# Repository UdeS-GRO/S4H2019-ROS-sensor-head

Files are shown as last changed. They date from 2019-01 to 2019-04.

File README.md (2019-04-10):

# 3-axes-Camera-ROS

## Introduction

3 axis head system that can be controlled by a cell phone or a USB controller. This open-source project is part of the Robotics Engineering Project Course at the Université de Sherbrooke.

Useful links: 

- http://emanual.robotis.com/docs/en/software/dynamixel/dynamixel_workbench/#ros
- http://emanual.robotis.com/docs/en/parts/controller/opencr10/#install-on-linux
- https://github.com/GoldenCheetah/GoldenCheetah/wiki/Allowing-your-linux-userid-permission-to-use-your-usb-device

# 1- Linux configuration

## Update

If you start from a clean Linux install, please do the following commands. 

```bash
$ sudo apt-get update
$ sudo apt-get upgrade
```

## USB Port Permissions

In order to communicate with the OpenCR card via USB, the user has to be added to the correct group. This [link](https://github.com/GoldenCheetah/GoldenCheetah/wiki/Allowing-your-linux-userid-permission-to-use-your-usb-device) shows all the details about this modification. But don't forget this part: **Important: the computer needs to be restarted to have the modifications applied.**

```bash
[user@machine ~]$ sudo usermod -a -G dialout user
```

## Arduino IDE

See http://emanual.robotis.com/docs/en/parts/controller/opencr10/#install-on-linux for instructions to use the full and latest version of the Arduino IDE, not the one in the packages repository since it might be updated.

# 2- OpenCR board configuration

To be able to control the Dynamixel motors via ROS, the OpenCR card need to be converted in a USB to Serial device that will make the bridge between the ROS server (on Linux) and the motors connected with the OpenCR card. 

After Arduino IDE is run, click File → Preferences in the top menu of the IDE. When the Preferences window appears, copy and paste the following link to the Additional Boards Manager URLs text box.

```bash
https://raw.githubusercontent.com/ROBOTIS-GIT/OpenCR/master/arduino/opencr_release/package_opencr_index.json
```

Then, click Tools → Board → Boards Manager. Type OpenCR into the text box to find the OpenCR by ROBOTIS package. When you find it, click Install. After the installation, “INSTALLED” will appear on your screen. See if the OpenCR Board is now on the list of Tools → Board. Click this to import the OpenCR Board source.

## Code upload

In order to the OpenCR card to make the bridge, please upload `usb_to_dxl` firmware (`File` -> `Examples` -> `OpenCR` -> `10.Etc` -> `usb_to_dxl`) Then you can use `/dev/ttyACM0` port (The number of the port may be different depending on setup).

## Hardware

In order to test the motors, please connect a SINGLE motor, connect the power supply and power on the card. 

# 3- ROS Installation

You can follow this [link](http://emanual.robotis.com/docs/en/software/dynamixel/dynamixel_workbench/) for the installation tutorial. The ROS utilization corresponds to the section 5 of the tutorial. Below are the condensed steps that need to be taken. Below are the simplified steps. 

## Install ROS on PC

The following script will allow you to simplify the ROS installation procedure. Run the following command in a terminal window. 

```bash
wget https://raw.githubusercontent.com/ROBOTIS-GIT/robotis_tools/master/install_ros_kinetic.sh && chmod 755 ./install_ros_kinetic.sh && bash ./install_ros_kinetic.sh
```

**After install ROS, please reboot PC**

## Download ROS Packages

Once ROS is installed, you'll need to change the directory to catkin_ws/src. It is where all the ROS package will be installed. 

```bash
cd ~/catkin_ws/src
```

**Main packages**

```bash
git clone https://github.com/ROBOTIS-GIT/dynamixel-workbench.git
git clone https://github.com/ROBOTIS-GIT/dynamixel-workbench-msgs.git
```

**Dependant packages**

```bash
git clone https://github.com/ROBOTIS-GIT/DynamixelSDK.git
git clone https://github.com/ROBOTIS-GIT/open_manipulator_msgs.git
sudo apt-get install ros-kinetic-moveit-core ros-kinetic-moveit-ros-planning ros-kinetic-moveit-ros-planning-interface
```

**Install this package**

Still in the ```catkin_ws/src/``` folder, clone this project.
```bash
git clone https://github.com/gene2302/3-axis-ROS-sensor-head.git
```

Once all the git has been cloned, different ROS packages will be installed too. 

## ROS Initilization

First, you'll need to source the correct ROS workspace in order to use ROS from anywhere. Then, make sure all dependencies are installed by using the rosdep tool. Finally, run catkin_make to build all the ROS workspace. 

```bash
source /opt/ros/kinetic/setup.bash
cd ~/catkin_ws
sudo apt-get update
rosdep install --from-paths src --ignore-src -r -y
catkin_make
```

If you are using a Raspberry Pi or a computer low on memory, you might need to limit the number of build threads jobs launched my catkin_make. By default, catkin_make launches one job (thread) per processor core. The `-j 1` argument and value specifies to run one job. It will be slower, but will compile.

```bash
source /opt/ros/kinetic/setup.bash
cd ~/catkin_ws
sudo apt-get update
rosdep install --from-paths src --ignore-src -r -y
catkin_make -j 1
```

# 4- ROS Use for a single motor

## Find the Dynamixels connected to the OpenCR card. 

In order to see which Dynamixel motors are connected, this command needs to be executed. Change ''ACM0'' to the port used by the OpenCR card. 

```bash
rosrun dynamixel_workbench_controllers find_dynamixel /dev/ttyACM0
```

## Control a SINGLE motor with ROS (command line)

**WARNING**: This package is intended for `SINGLE` Dynamixel. Please connect only `One(1)` Dynamixel to your device. If you connect multiple Dynamixels, manager would detect the **lowest ID** among connected Dynamixels. This package is to check Dynamixel status and access Dynamixel’s control table. 

## Control a SINGLE motor with ROS (GUI)

Important: In order to connect this node with the connect USB port, you shall modify the port in the configuration file located in the dynamixel_workbench_controllers config file. When using the ```sensor_head_gui``` package, the dynamixel_workbench_controllers configuration file does not need to be changed here, as it is supplied by the ```sensor_head_gui.launch``` file located in  ```ROS/sensor_head_gui/launch/sensor_head_gui.launch```

```bash
roslaunch dynamixel_workbench_single_manager single_manager.launch
```

This package is to check Dynamixel status and access Dynamixel’s Control Table addresses via **GUI**. **WARNING**: Before you run this package, please launch [single_manager](http://emanual.robotis.com/docs/en/software/dynamixel/dynamixel_workbench/#single-manager) first.

```
rosrun dynamixel_workbench_single_manager_gui dynamixel_workbench_single_manager_gui
```

# 5- Using "sensor_head_gui" package

In order to use the package, please launch this launch file.

```
roslaunch sensor_head_gui base_launch.launch
```

This file will launch several ROS nodes (dynamical_workbench_controllers, sensor_head_gui). If you can't find the package, please see https://answers.ros.org/question/190317/ros-cant-find-package/

The arguments in this file, as well as the two .yaml configuration files in the ```ROS/sensor_head_gui/config/``` folder, can be modified with other values if your setup is different.

Before the first run, a certificate must be created to be able to use a secured (https) website, required to use motion sensors on a mobile device. Create a SSL certificate by filling out the answers to the informations asked by the program, and make sure to use the exact name (address) that will be used at the FQDN or YOUR name question:
```
cd ~ && openssl req -new -x509 -keyout s4e4gro.pem -out s4e4gro.pem -days 365 -nodes
```

Using a https connection is required to use the orientation and motion javascript interfaces, or else they do not work, since it was deprecated. The certificate file is not included in the source control. 

You can now open a browser to "https://localhost:4443" or replace localhost with the host's IP adress, or the computer's name if the full names are resolved. Adding the https is important.

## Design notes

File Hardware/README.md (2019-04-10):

# Assembly Process

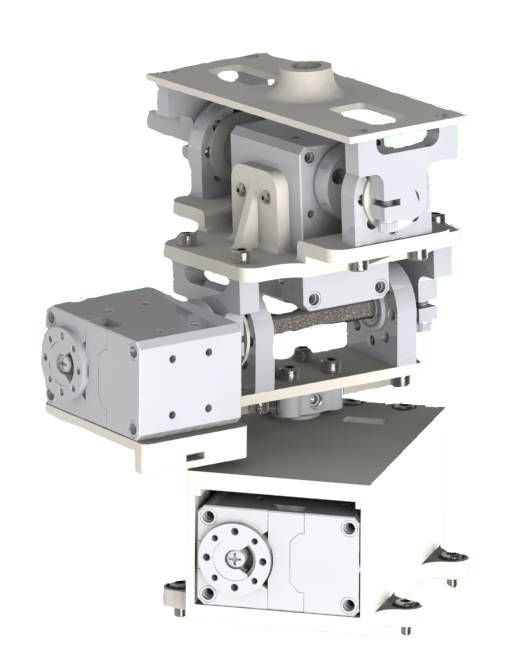
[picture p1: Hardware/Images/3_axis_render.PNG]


## 1 - Download BOM.
Download the build of material, follow this link : 
[Excel BOM](https://github.com/gene2302/3-axis-ROS-sensor-head/blob/master/Hardware/BOM/Master_parts_list.xlsx)

## 2 - Purchase required standards parts.

You need purchase some standard parts from Servocity, Dynamixel and McMaster for exemple. All links are in the BOM excel.

## 3 - 3D print all 3d printed parts

You need to print all pieces and respect qty. 

Caracteritics for PLA printing:

Layer high : 0,2mm
Extruder temp: 195-205 degC
Infill : 10 to 60 % Diamond infill

## 4 - Assembly the Z module:

Take the Z motor, fix the adapter_gear on the motor with 4 screws m2.5.
Fix the bevel_gear on it. Screw the motor with the base. Fix the other bevel-gear on the 2in shaft. Place one bearing in the bearing hole. Place the other bearing in the top plate bearing hole. This is "pressfit" hole.
Finaly, join top plate with the base and srew it with 3X m3 SHCS.
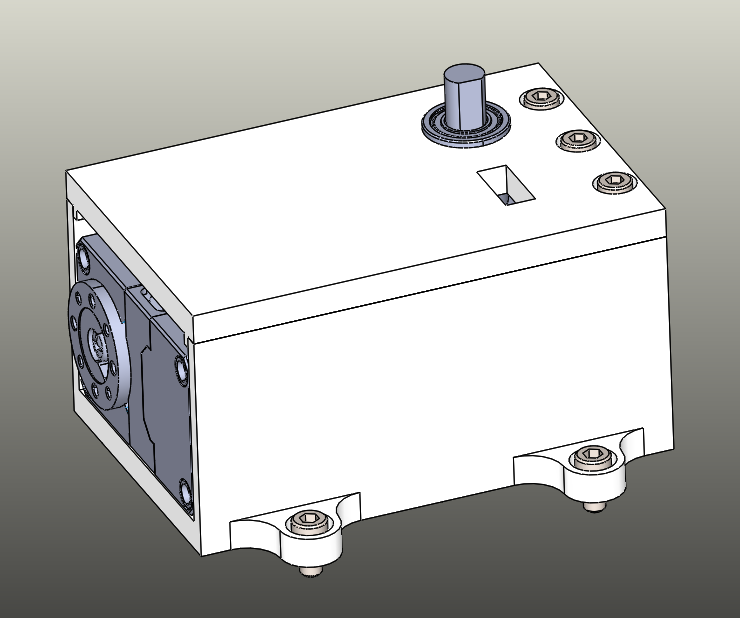
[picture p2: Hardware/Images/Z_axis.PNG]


## 5 - Assembly the X module:

Take the X motor (XM-430-w350) and screw the motor adaptor (item no ...). Place bearing support (2x) and spacer with screw #6-32(2x). Screw the shaft adaptor under the 3d printed piece with 4x #6-32.
Align shaft, bearing, spacer and ring for complete the assy.
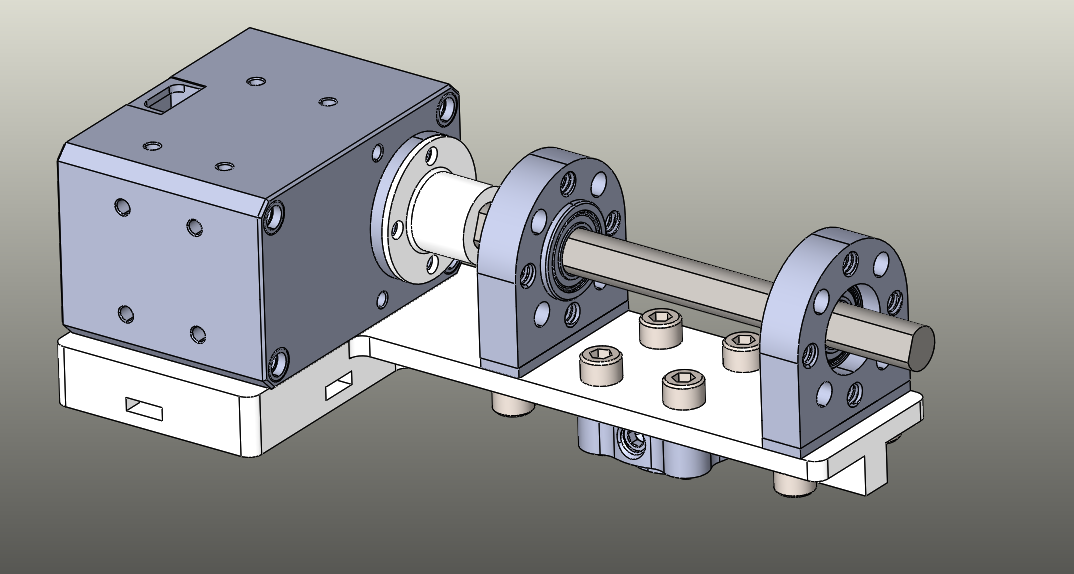
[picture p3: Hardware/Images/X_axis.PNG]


## 6 - Assembly the Y module:

Take the Y motor(XM-430-w250) and screw the motor adaptor on it. Plug 1in shaft in the adaptor motor. Next, screw 2x bearing supports and 2x bore bottom with the 3d printed y-plate (#6-32). Place the other shaft with a collet and spacer.
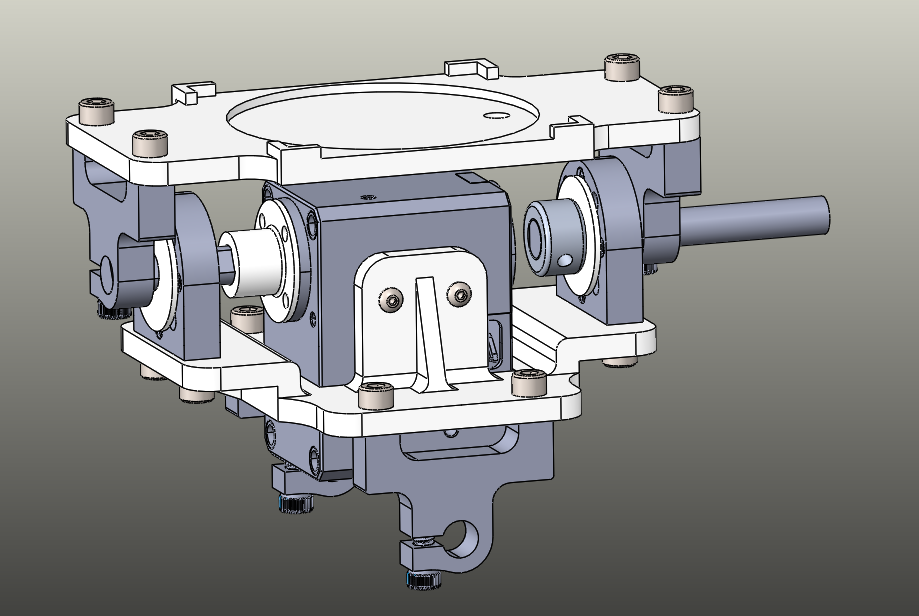
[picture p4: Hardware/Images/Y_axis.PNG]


## 7 - Assembly the full module.

Take all the modules and assemble them together with appropriates screws according with the picture.
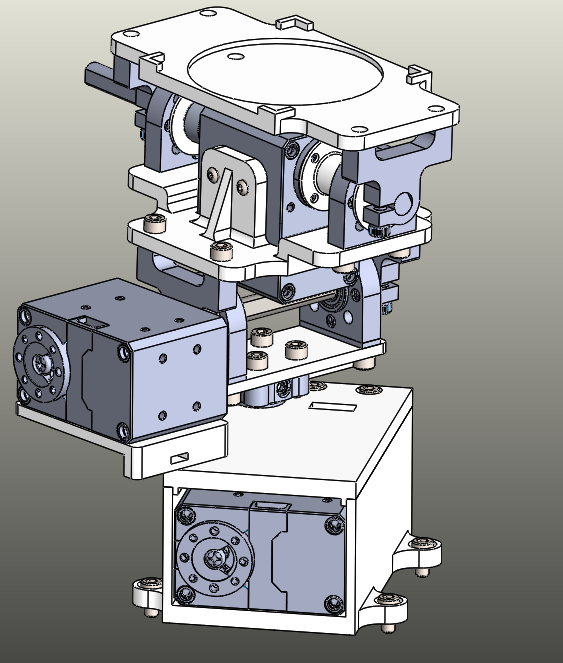
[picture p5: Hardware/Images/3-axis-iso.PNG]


<!--stackedit_data:
eyJoaXN0b3J5IjpbLTE4NjkwNDc1NTUsLTM2NjI4Njg2MSw0ND
A3NjIyMTcsLTIyNjI0MTQwMiwtMjM4MTM3MzU2LC0xNDYwMzQ3
OTA3LC0xMjY1MTA3ODQ0LDE3ODg3OTc0MDMsMTkyMTkzNDQ0Ny
wtNTU0MDY0NjA2LC0zNDU2NDMzNDQsMTEyMDA1NTk5XX0=
-->

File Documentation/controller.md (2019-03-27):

http://wiki.ros.org/joy/Tutorials/ConfiguringALinuxJoystick

Install the xbox controller driver with:
```bash
sudo apt-get install xboxdrv
```

Add controller in the USB ports of Virtualbox
Check if it is there with 
```bash
lsusb
```
then install joy with
```bash
sudo apt-get install ros-kinetic-joy
ls /dev/input/
```

Test to see which port your controller is attached to like this for example:

```bash
sudo jstest /dev/input/js2
```
Here's the mapping for our Xbox One Controller
* Axes:
	* 0: Left Joystick L/R (Analog) L = 1, R = -1
	* 1: Left Joystick U/D (Analog) U = 1, D = -1
	* 2: LT (Analog) Not pressed = 1 Max = -1
	* 3: Right Joystick L/R (Analog)
	* 4: Right Joystick U/D (Analog)
	* 5: RT (Analog)
	* 6: Cross L/R (Digital)
	* 7: Cross U/D (Digital)

* Buttons (Digital): (0 or 1)
	* 0: A
	* 1: B
	* 2: X
	* 3: Y
	* 4: L
	* 5: R
	* 6: Back
	* 7: Start
	* 8: Power
	* 9: Pressing Left Joystick
	* 10: Pressing Right Joystick

You have to make the joystick accesible to ROS with:

```bash
sudo chmod a+rw /dev/input/js2
ls -l /dev/input/js2
```

then run joy to see values of your axes and buttons that should be between -1 and 1

In different terminals, run:
```bash
roscore
```
```bash
rosparam set joy_node/dev "/dev/input/js2"
rosrun joy joy_node
``` 
and
```bash
rostopic echo joy
```

then follow the tutorial at: http://wiki.ros.org/joy/Tutorials/WritingTeleopNode
but add 
```bash
catkin_package()
```
in the CMakeLists.txt file

also do a

```bash
catkin_make
```
and source your bash

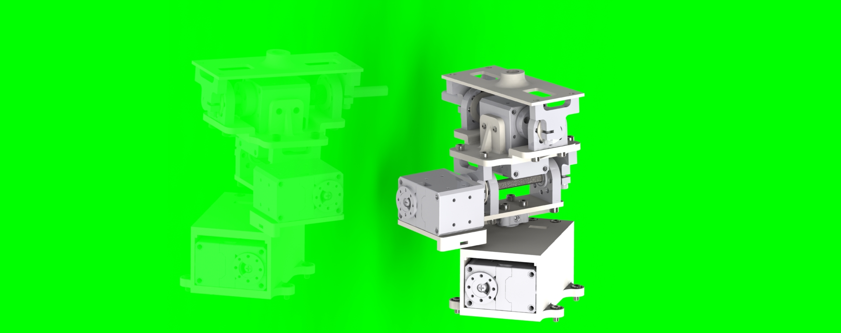
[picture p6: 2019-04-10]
Hardware/Images/rendu vert.JPG

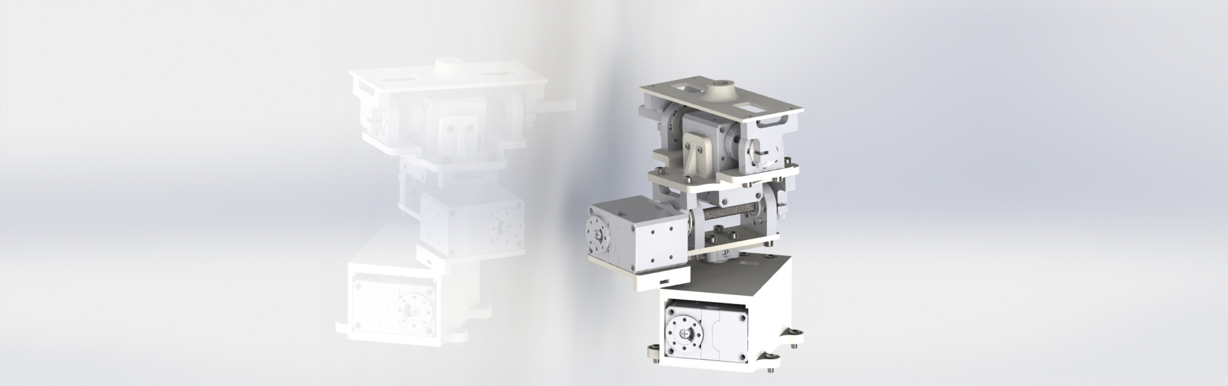
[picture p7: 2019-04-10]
Hardware/Images/rendu blanc.JPG

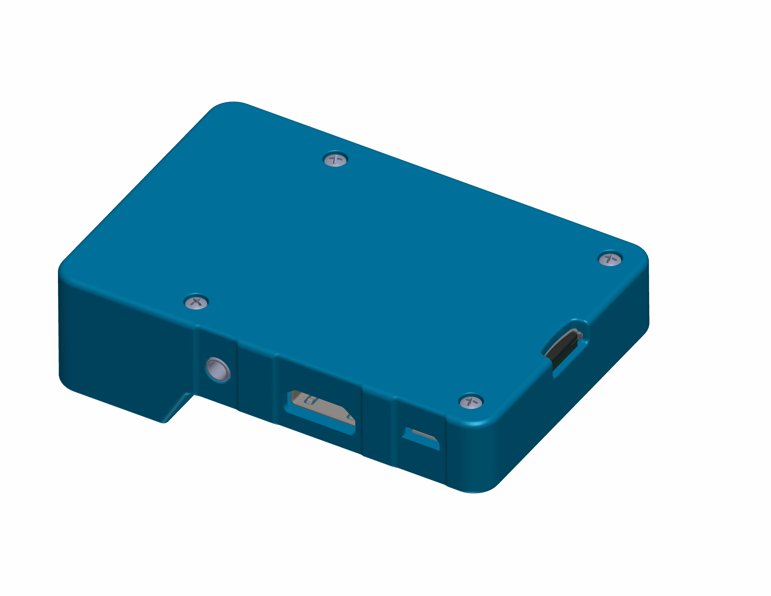
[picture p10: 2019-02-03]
Hardware/CAD/raspberry-pi-b-case-1.snapshot.3/RPI B+ Case Bottom View.JPG

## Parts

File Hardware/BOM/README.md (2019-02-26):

## Build of materiel:

This is the BOM for assembly the head module. 
You can buy all stuf by internet, follow links in the excel.

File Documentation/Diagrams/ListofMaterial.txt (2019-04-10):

List of material:
Raspberry Pi 3B+
USB Camera (We used Microsoft LifeCam VX-2000)
OpenCR 1.0
Dynamixel Motor XL430-W250-T (2)
Dynamixel Motor XM430-W350-T
Xbox One Controller
Android Cell Phone
Mouse
Screen
Keyboard

Raspberry Pi Power Supply (Type A - Micro-USB)
OpenCR Power Supply (Type A - Coaxial)
3-pin connector(3)
USB-USB cable
HDMI-HDMI cable

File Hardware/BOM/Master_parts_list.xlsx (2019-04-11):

The cost information contained in this document is of a budgetary and planning nature and is intended for informational purposes only.
Author: Etienne Gendron, Robotic engineering |  |  |  |  |  |  |  | Total | $473.08
University of Sherbrooke, QC, CAN
Part | Qty in sub-assy | Qty to Print | Qty In project | Brand | Ref | Model/Config (If applicable) | Project Section | Price | Cost to Project | Link
Z_Assy | - | - | 1
Z_base | - | 1 | 1 | 3Dprinting |  |  |  | $12.00 | $12.00
Cover | - | 1 | 1 | 3Dprinting |  |  |  | $6.00 | $6.00
adapter moteur-gear | - | 1 | 1 | 3Dprinting |  |  |  | $1.00 | $1.00
bearing | 2 | - | 6 | Servocity | 535198 |  | 5.78 $ | $2.89 | $17.34 | https://www.servocity.com/0-250-id-x-0-500-od-flanged-ball-bearing
XL-430-w250 | 1 | - | 2 | Dynamixel |  |  | 49.90 $ | $49.90 | $99.80 | http://www.robotis.us/dynamixel-xl430-w250-t/
gear_45 | 2 | - | 2 | Servocity | 615406 |  | 11.98 $ | $5.99 | $11.98 | https://www.servocity.com/6mm-bevel-gears
shaft_0.25-2 | 1 | - | 1 | Servocity | 634068 |  | 1.49 $ | $1.49 | $1.49
SHCS (B18.3.1M - 2.5 x 0.45 x 5) | 4 | - | 4 | hardware
SHCS (B18.3.1M - 3 x 0.5 x 5) | 3 | - | 3 | hardware
HEX_NUT_M3 | 3 | - | 3 | hardware
HX-SHCS (0.138-32x0.25x0.25-N) | 4 | - | 4 | hardware
X_Assy |  |  | 1
X_base_3.0 | - | 1 | 1 | 3Dprinting |  |  |  | $8.00 | $8.00
spacer_plat | - | 2 | 2 | 3Dprinting |  |  |  | $1.00 | $2.00
adapter moteur shaft_gros moteur | - | 1 | 1 | 3Dprinting |  |  |  | $1.00 | $1.00
Bearing spacer | - | 2 | 4 | 3Dprinting |  |  |  | $1.00 | $4.00
XM-430-W350 | 1 | - | 1 | Dynamixel | 902-0124-000 |  | 229.90 $ | $229.90 | $229.90 | http://www.robotis.us/dynamixel-xm430-w350-t/
bearing support bas | 2 |  | 4 | servocity | 545412 |  | 8.98 $ | $4.49 | $17.96
bearing | 2 |  | 6 | servocity | 535198 |  | 5.78 $ | $2.89 | -
0.25_hub | 1 |  | 1 | servocity | 545548 | 0.770" Pattern Set Screw Hubs | 4.99 $ | $4.99 | $4.99 | https://www.servocity.com/770-set-screw-hubs
shaft_0.25_3po | 1 |  | 1 | servocity | 634078 | 0,250 * 3po | 1.99 $ | $1.99 | $1.99 | https://www.servocity.com/0-250-1-4-stainless-steel-d-shafting
SHCS (0.138-32x0.4375x0.4375-N) | 4 |  | 4 | hardware
SHCS (0.138-32x0.3125x0.3125-N) | 4 |  | 16 | hardware
SHCS (B18.3.1M - 2.5 x 0.45 x 4) | 4 |  | 4 | hardware
Y_Assy |  |  | 1
Y Top_plate_V2 | - | 1 | 1 | 3Dprinting |  |  |  | $12.00 | $12.00
adapter moteur shaft | - | 1 | 1 | 3Dprinting |  |  |  | $1.00 | $1.00
Bearing spacer | - | 2 | 4 | 3Dprinting |  |  |  | $1.00 | $4.00
Sensor_plate | - | 1 | 1 | 3Dprinting |  |  |  | $8.00 | $8.00
XL-430-w250 | 1 |  | 2 | Dynamixel |  |  | 49.90 $ | $49.90 | - | http://www.robotis.us/dynamixel-xl430-w250-t/
bearing support bas | 2 | - | 4 | servocity | 545412 |  | 8.98 $ | $4.49 | - | https://www.servocity.com/90-hub-mount-a
0.25 Bore Bottom Tapped Clamping Mount | 4 | - | 4 | servocity | 585542 | 1/4" (0.25") | 23.96 $ | $5.99 | $23.96 | https://www.servocity.com/1-4-bottom-tapped-clamping-mount
bearing | 2 | - | 6 | servocity | 535198 |  | 5.78 $ | $2.89 | -
shaft_0.25-1po | 2 | - | 2 | servocity | 634058 |  | 1.98 $ | $0.99 | $1.98 | https://www.servocity.com/0-250-1-4-stainless-steel-d-shafting
SHCS (0.138-32x0.3125x0.3125-N) | 12 | - | 16 | Hardware
SBHCSCREW (0.086-56x0.25-HX-N) | 4 | - | 4 | Hardware
Collet 1_4 | 1 | - | 1 | servocity | 6432K12 | 1/4"-10-32 | $1.00 | $1.00 | $1.00 | https://www.servocity.com/steel-set-screw-collars
Spacers_0.25 | 1 |  | 1 | servocity | 633104 |  | $1.69 | $1.69 | $1.69 | https://www.servocity.com/shafting-and-tubing-spacers
 |  |  |  | FM | 10

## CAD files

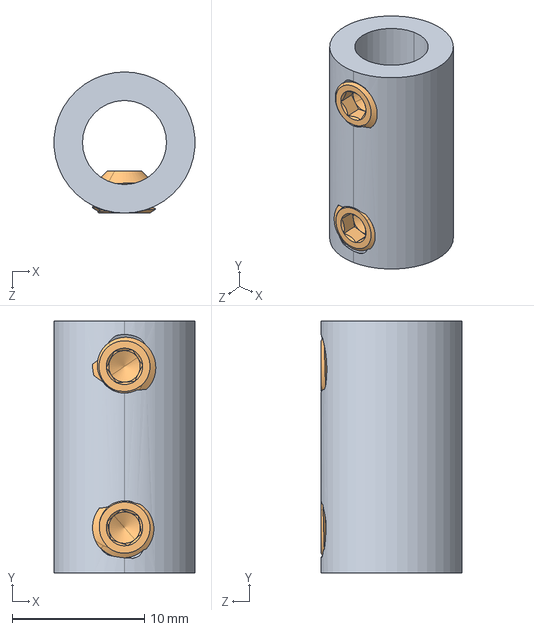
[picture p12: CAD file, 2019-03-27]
Hardware/CAD/3_axes_cad/Standards parts/join_coupling.SLDASM
10.6 x 19.1 x 10.7 mm
625104.STEP
632134_91375A436.STEP x 2

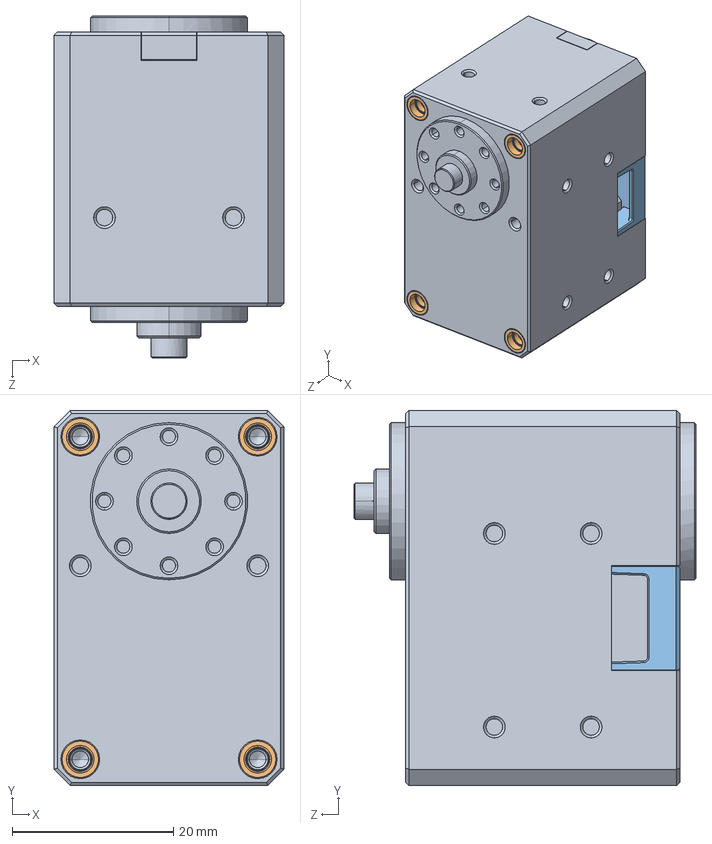
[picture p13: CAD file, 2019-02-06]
Hardware/CAD/3_axes_cad/Standards parts/Motors/XM-430-W350.SLDASM
28.5 x 46.5 x 42.4 mm
X-430_IDLE.stp
X-430_SPACER_RING.stp x 8
X-430_CVR_CABLE.stp

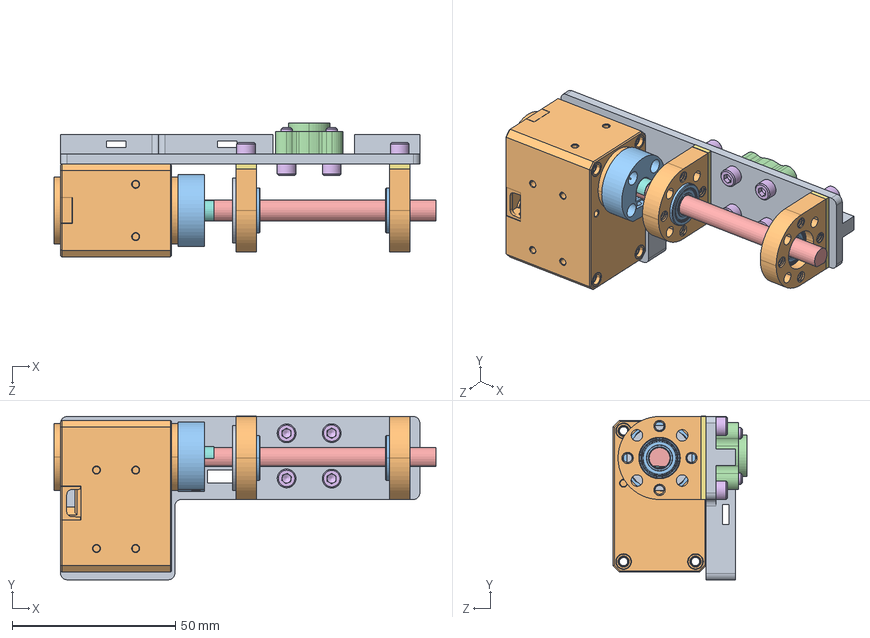
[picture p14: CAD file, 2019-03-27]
Hardware/CAD/3_axes_cad/X_Assy.SLDASM
116.9 x 50.1 x 41.0 mm
X_base_3.0
bearing support bas x 2
bearing x 2
0.25_hub
shaft_0.25_3po
socket head cap screw_ai x 8
spacer_plat x 2
Bearing spacer
XL-430-w250
Coupler_MotorV3_big

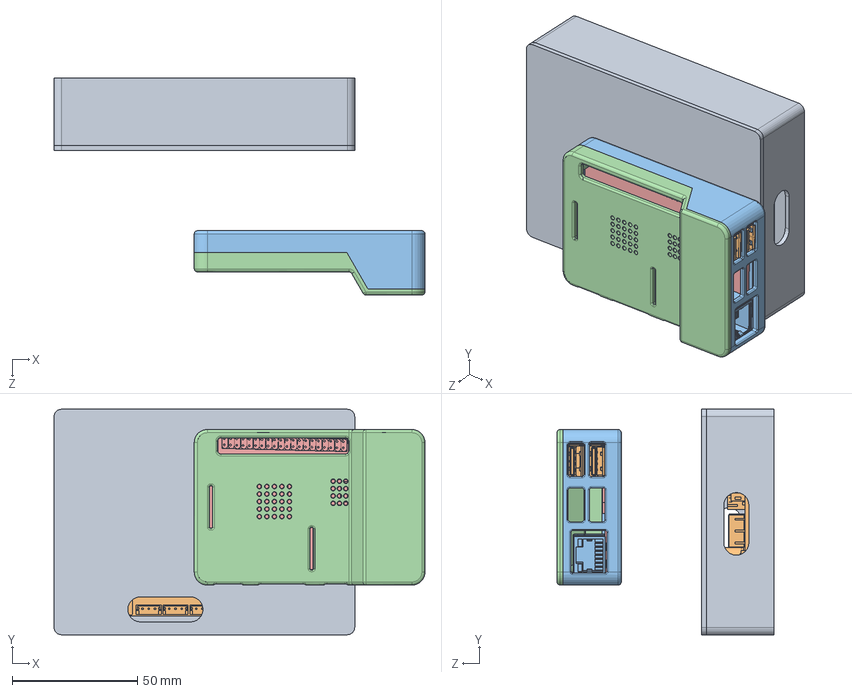
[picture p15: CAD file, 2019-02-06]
Hardware/CAD/OpenCR/Parts/OpenCR_case.SLDASM
148.0 x 90.0 x 86.6 mm
CaseOpenCR
OpenCR-1
Cover_OpenCR_CASE

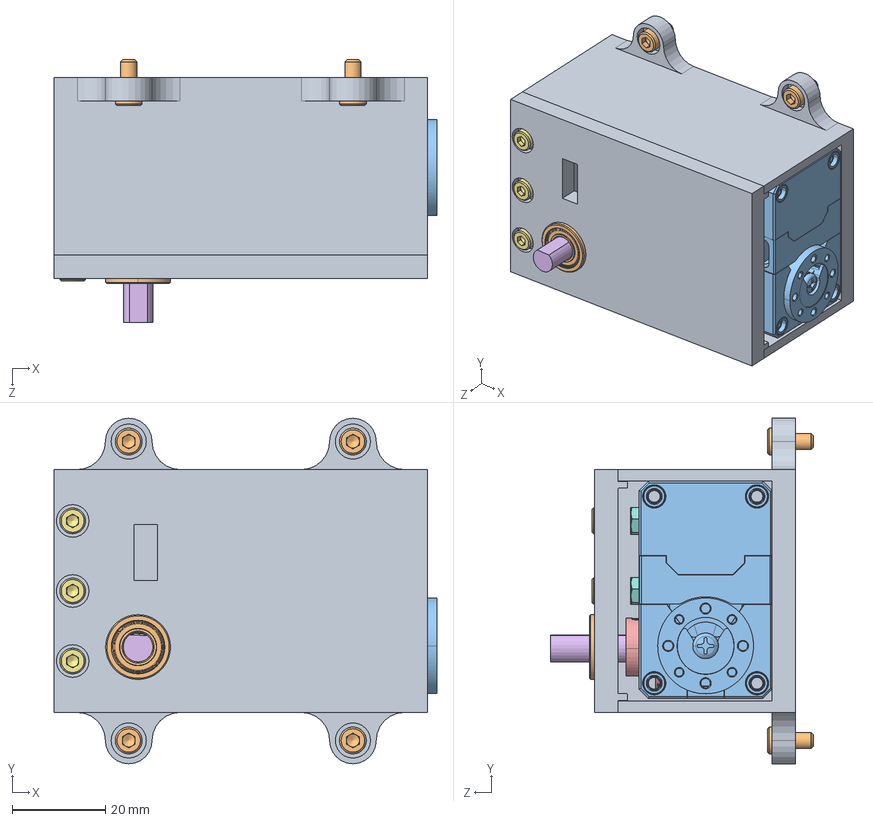
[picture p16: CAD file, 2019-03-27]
Hardware/CAD/3_axes_cad/Z_Assy.SLDASM
82.0 x 74.0 x 56.2 mm
Z_base
bearing x 2
XL-430-w250
adapter moteur-gear
gear_45 x 2
shaft_0.25-2
socket head cap screw_am x 7
90591A250_ZINC PLATED STEEL HEX NUT x 3
socket head cap screw_ai x 4

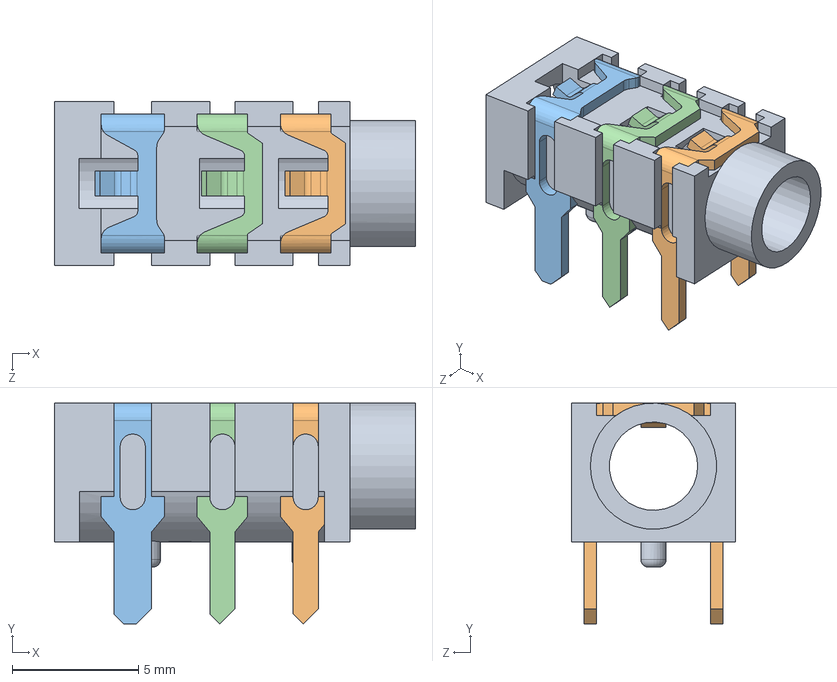
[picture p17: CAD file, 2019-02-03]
Hardware/CAD/raspberry-pi-b-case-1.snapshot.3/pi/PCB_Stereo_Jack_(assembly).SLDASM
14.3 x 8.75 x 6.50 mm
PCB_Stereo_Jack_(body)
PCB_Stereo_Jack_(GND_contact)
PCB_Stereo_Jack_(channel_contact_2)
PCB_Stereo_Jack_(channel_contact_1)

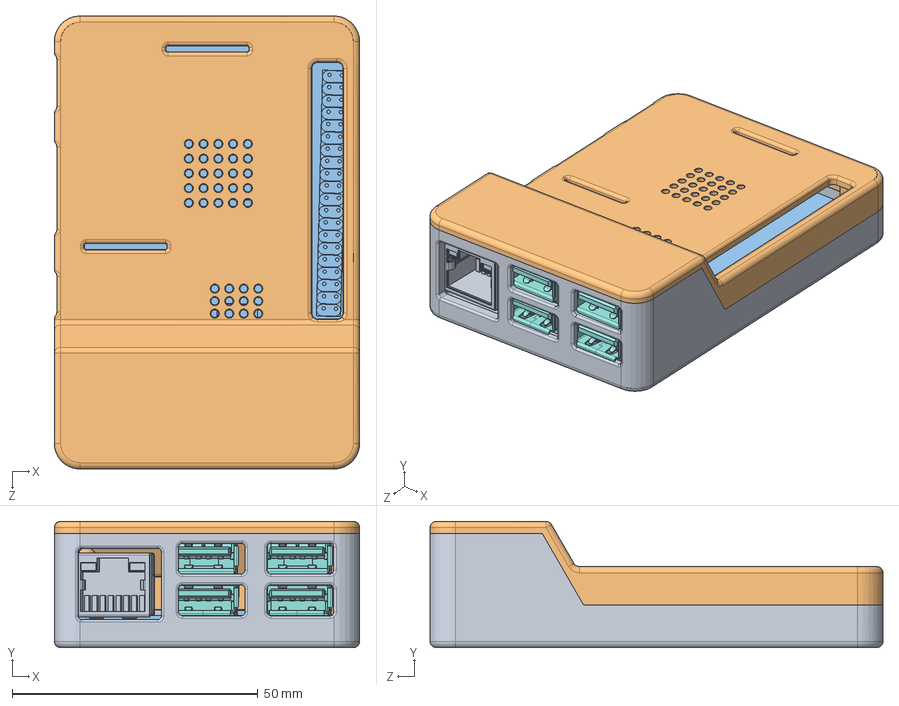
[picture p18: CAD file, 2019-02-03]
Hardware/CAD/raspberry-pi-b-case-1.snapshot.3/RPI B+Case Assy.SLDASM
62.1 x 25.7 x 92.1 mm
RPI B+ Case Bottom
RPI B+ Case Top
carte_mere
HDMI_socket_cover
HDMI_socket_inside
HDMI_socket_large_pin x 10
HDMI_socket_small_pin x 9
usb3x2 x 2
RJ45_10P_TJ3009
PCB_Stereo_Jack_(body)
PCB_Stereo_Jack_(GND_contact)
PCB_Stereo_Jack_(channel_contact_2)
PCB_Stereo_Jack_(channel_contact_1)
USB

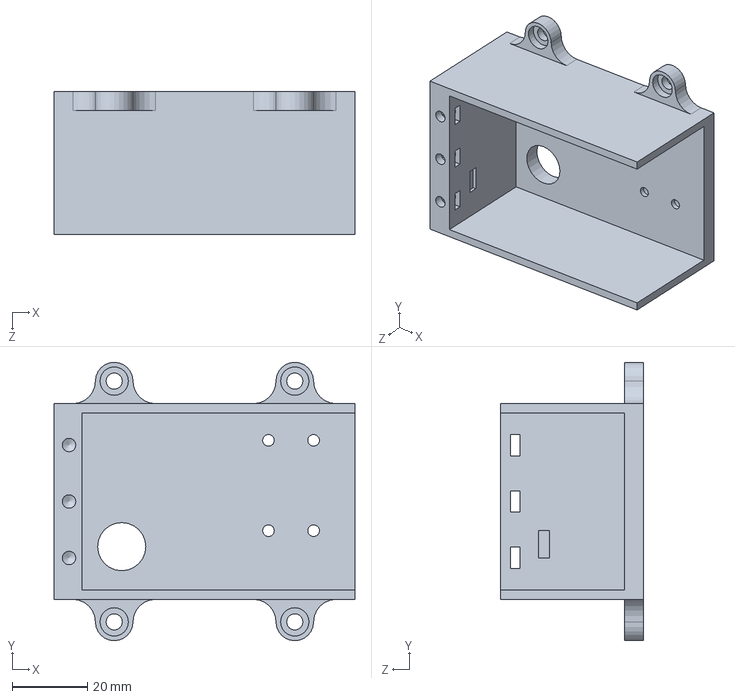
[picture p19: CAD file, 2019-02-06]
Hardware/CAD/3_axes_cad/Full_Assy.SLDASM
80.0 x 74.0 x 38.0 mm

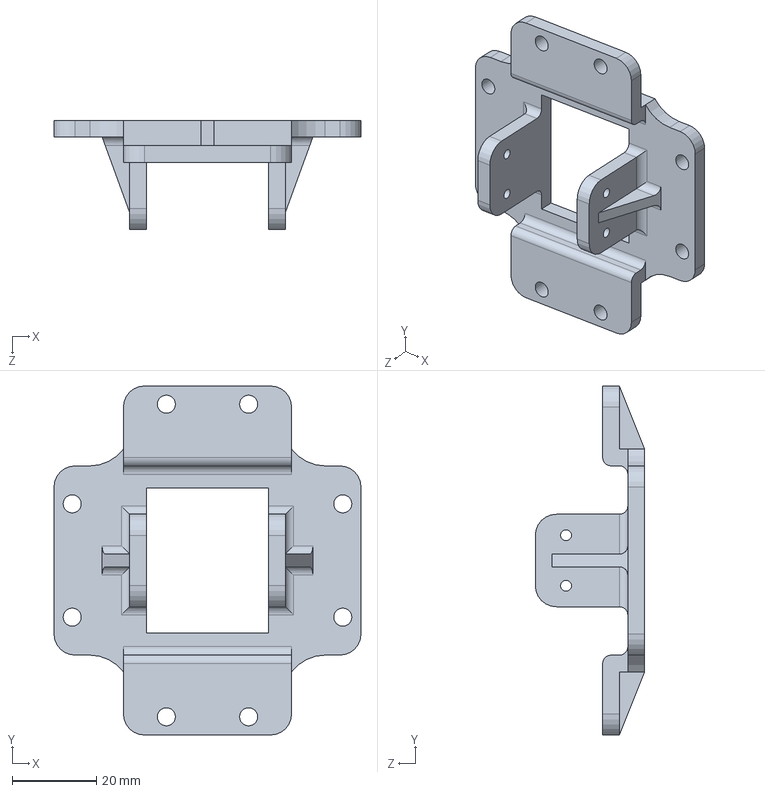
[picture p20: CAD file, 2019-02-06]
Hardware/CAD/3_axes_cad/Y_Assy.SLDASM
73.0 x 83.0 x 26.0 mm

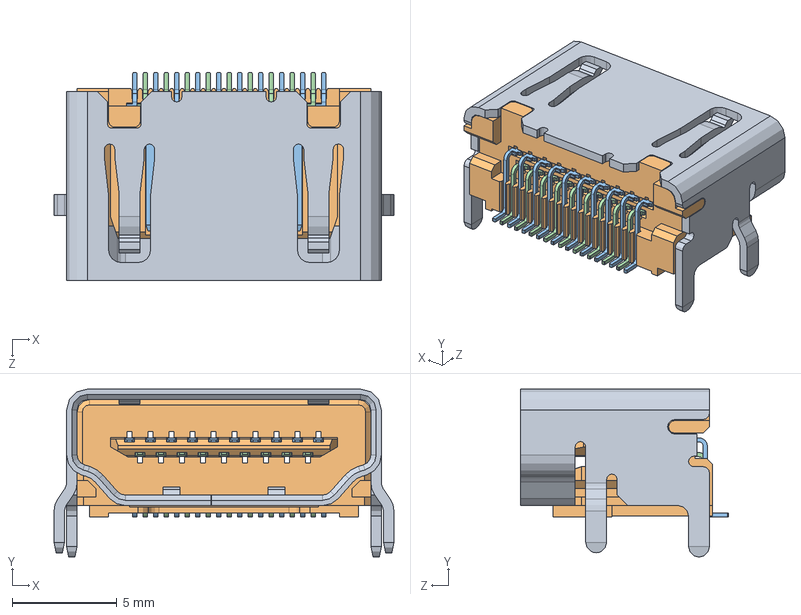
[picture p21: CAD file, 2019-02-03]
Hardware/CAD/raspberry-pi-b-case-1.snapshot.3/pi/hdmi/HDMI_socket.SLDASM
16.2 x 8.00 x 9.90 mm
HDMI_socket_cover
HDMI_socket_inside
HDMI_socket_large_pin x 10
HDMI_socket_small_pin x 9

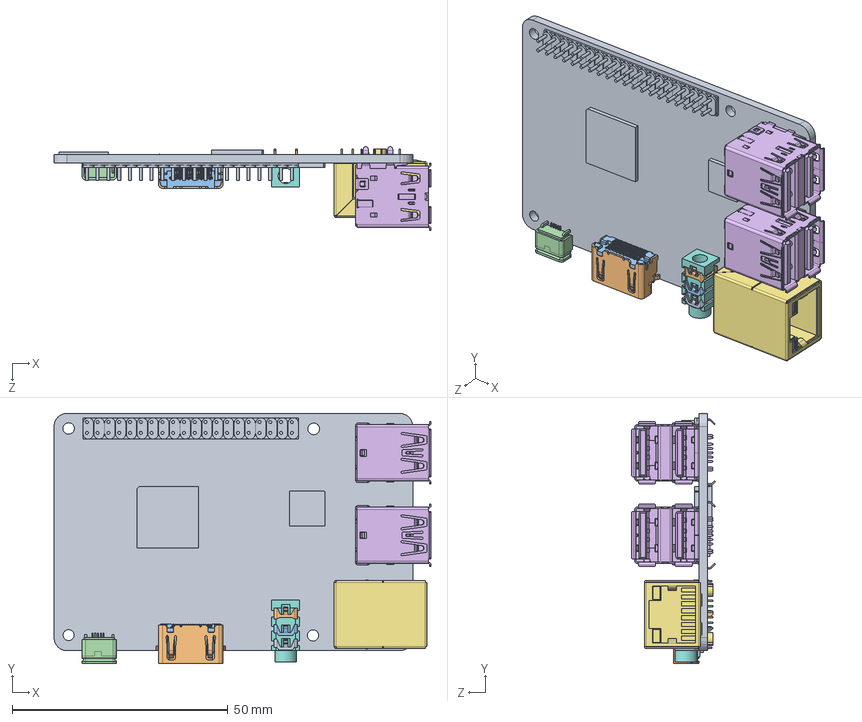
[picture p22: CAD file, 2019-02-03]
Hardware/CAD/raspberry-pi-b-case-1.snapshot.3/pi/raspberry_carte.SLDASM
87.4 x 58.0 x 19.4 mm
carte_mere
HDMI_socket_cover
HDMI_socket_inside
HDMI_socket_large_pin x 10
HDMI_socket_small_pin x 9
usb3x2 x 2
RJ45_10P_TJ3009
PCB_Stereo_Jack_(body)
PCB_Stereo_Jack_(GND_contact)
PCB_Stereo_Jack_(channel_contact_2)
PCB_Stereo_Jack_(channel_contact_1)
USB

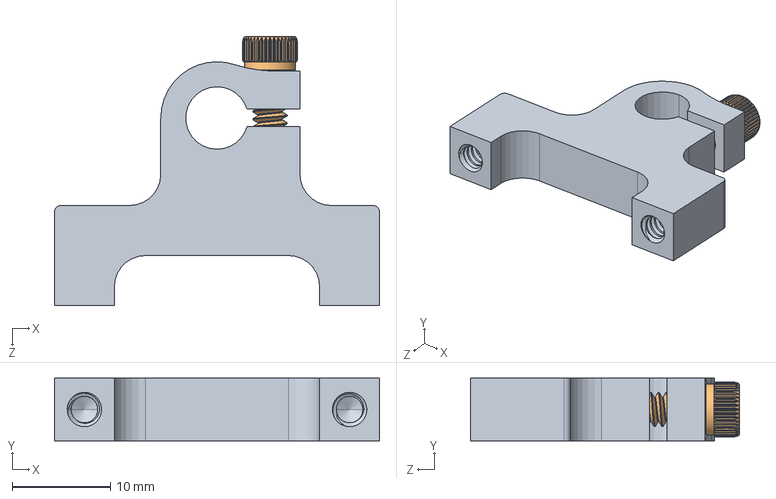
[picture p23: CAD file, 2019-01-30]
Hardware/CAD/3_axes_cad/Standards parts/0.25 Bore Bottom Tapped Clamping Mount.SLDASM
33.0 x 6.35 x 27.3 mm
585542.STEP
632110_90128A121.STEP

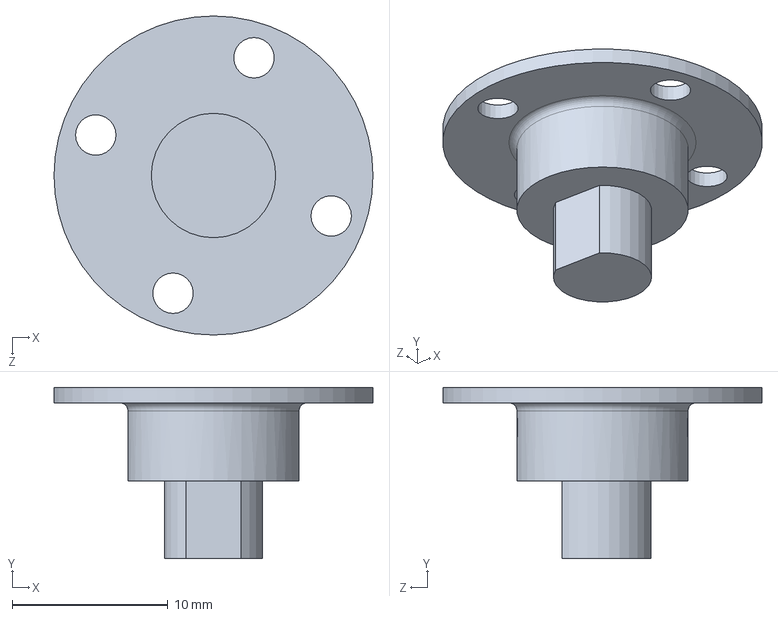
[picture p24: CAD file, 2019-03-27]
Hardware/CAD/3_axes_cad/3D_printed_parts/adapter moteur shaft_gros moteur.sldprt
20.5 x 11.0 x 20.5 mm

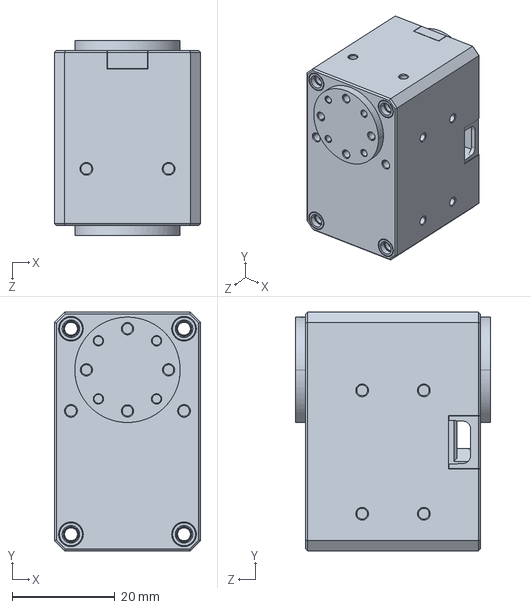
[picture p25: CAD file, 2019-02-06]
Hardware/CAD/3_axes_cad/Standards parts/Motors/XL430_W250/XL-430-w250.SLDPRT
28.5 x 46.5 x 38.0 mm

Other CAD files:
Hardware/CAD/OpenCR/3D printed/Cover_OpenCR_CASEV1.STL
Hardware/CAD/OpenCR/Parts/Cover_OpenCR_CASE.SLDPRT
Hardware/CAD/raspberry-pi-b-case-1.snapshot.3/pi/hdmi/HDMI_socket_inside.SLDPRT
Hardware/CAD/raspberry-pi-b-case-1.snapshot.3/pi/PCB_Stereo_Jack_(channel_contact_1).SLDPRT
Hardware/CAD/3_axes_cad/3D_printed_parts/Bearing spacer.sldprt
Hardware/CAD/3_axes_cad/3D_printed_parts/Coupler_MoteurV2.sldprt
Hardware/CAD/3_axes_cad/3D_printed_parts/Coupler_MotorV3_big.sldprt
Hardware/CAD/3_axes_cad/3D_printed_parts/Cover.sldprt
Hardware/CAD/3_axes_cad/3D_printed_parts/STL/Bearing spacer.STL
Hardware/CAD/3_axes_cad/3D_printed_parts/STL/Coupler_MoteurV2.STL
Hardware/CAD/3_axes_cad/3D_printed_parts/STL/Coupler_MotorV3_big.STL
Hardware/CAD/3_axes_cad/3D_printed_parts/STL/Y Top_plate.STL
Hardware/CAD/3_axes_cad/3D_printed_parts/STL/Y Top_plate_v2.STL
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

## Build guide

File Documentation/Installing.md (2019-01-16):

# Installing and configuring ROS on the Raspberry Pi

Ubuntu MATE 16.04 (Xenial) and ROS Kinetic are used to ensure compatibility for when a pi-gen script will be used to create the images. Currently, pi-gen does not support Ubuntu Bionic, required for ROS Melodic. 

## Installing Ubuntu MATE 16.04

Ubuntu MATE 16.04 should be downloaded and installed on the Raspberry Pi.
<https://ubuntu-mate.org/raspberry-pi/>

## Installing ROS Kinetic

The procedure followed to install packages was from <http://wiki.ros.org/kinetic/Installation/Ubuntu>

Select the "Desktop Install" for the set of packages at step 1.4.
This might take some time (10-20 minutes or more) on the Raspberry Pi, since there is a lot of disk I/O.

See the file [installing_ros.bash](https://github.com/gene2302/3-axis-ROS-sensor-head/blob/master/installing_ros.bash) for the commands entered, or see below:
```bash
sudo sh -c 'echo "deb http://packages.ros.org/ros/ubuntu $(lsb_release -sc) main" > /etc/apt/sources.list.d/ros-latest.list'

sudo apt-key adv --keyserver hkp://ha.pool.sks-keyservers.net:80 --recv-key 421C365BD9FF1F717815A3895523BAEEB01FA116

sudo apt-get update
sudo apt-get install ros-kinetic-desktop

sudo rosdep init
rosdep update

echo "source /opt/ros/kinetic/setup.bash" >> ~/.bashrc
source ~/.bashrc

sudo apt install python-rosinstall python-rosinstall-generator python-wstool build-essential

printenv | grep ROS
```

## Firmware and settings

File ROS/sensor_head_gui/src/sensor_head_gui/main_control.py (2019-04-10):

#!/usr/bin/env python

import os
import sys
from functools import partial
from math import pi, atan2, asin

import rospkg
import rospy
from dynamixel_workbench_msgs.msg import *
from dynamixel_workbench_msgs.srv import *
from PyQt5 import *
from python_qt_binding import *
from rqt_gui.main import Main
from sensor_head_gui.msg import X_Controller
from sensor_head_gui.msg import HMI
from sensor_head_gui.msg import ControlSource
from std_msgs.msg import Int32, String
from geometry_msgs.msg import Vector3
from sensor_msgs.msg import Imu
from Constants import *
from Source import Source


class main_control():
    def __init__(self):
        """Initialisation function.
        """

        self.motor_range = {}
        self.motor_range['x'] = {}
        self.motor_range['x']['homeMot'] = 683
        self.motor_range['x']['homeAng'] = 0.0
        self.motor_range['x']['minPosMot'] = 0
        self.motor_range['x']['minPosAng'] = -(pi/3) * 2
        self.motor_range['x']['maxPosMot'] = 1535
        self.motor_range['x']['maxPosAng'] = (pi/3)*2
        self.motor_range['y'] = {}
        self.motor_range['y']['homeMot'] = 768
        self.motor_range['y']['homeAng'] = 0.0
        self.motor_range['y']['minPosMot'] = 0
        self.motor_range['y']['minPosAng'] = -(3*pi/8)*2
        self.motor_range['y']['maxPosMot'] = 1535
        self.motor_range['y']['maxPosAng'] = (3*pi/8)*2
        self.motor_range['z'] = {}
        self.motor_range['z']['homeMot'] = 2048
        self.motor_range['z']['homeAng'] = 0.0
        self.motor_range['z']['minPosMot'] = 0
        self.motor_range['z']['minPosAng'] = -pi
        self.motor_range['z']['maxPosMot'] = 4095
        self.motor_range['z']['maxPosAng'] = pi

        self.x = 0
        self.y = 0
        self.z = 0

        self.gyropos = [0, 0, 0]

        self.cellOn = False
        self.timer = 0
        self.currentSource = Source.Xbox  # Xbox

        rospy.on_shutdown(self.shutdown_hook)
        try:
            rospy.wait_for_service(
                '/dynamixel_workbench/dynamixel_command', 2)

            self.motor_proxy = rospy.ServiceProxy(
                '/dynamixel_workbench/dynamixel_command', DynamixelCommand,
                persistent=True)  # Enabled persistant connection

            self.subManette = rospy.Subscriber(
                "Xbox", X_Controller, self.callbackXbox, queue_size=2)

            # self.subMobileImuFiltered = rospy.Subscriber(
            #     "/mobile_imu_filtered", Imu, self.callbackMobile, queue_size=1)
            self.subMobileImuFiltered = rospy.Subscriber(
                "/mobile_imu", Imu, self.callbackMobile, queue_size=1)

            # self.subMobileImuFiltered = rospy.Subscriber(
            #     "/mobile_imu", Vector3, self.callbackMobile2, queue_size=1)
            self.subHMI = rospy.Subscriber(
                "/interface", HMI, self.callbackHMI, queue_size=1)

            self.subControlSource = rospy.Subscriber(
                "/control_source", ControlSource, self.callbackCtrlSrc, queue_size=10)

        except:
            print("WAIT")
            self.timer = rospy.Timer(rospy.Duration(2), self.connect)

        # Set max speed
        # self.commandMotor(1, "Position_P_Gain", 640)
        # self.commandMotor(2, "Position_P_Gain", 800)
        # self.commandMotor(3, "Position_P_Gain", 640)

        # self.commandMotor(1, "Torque_Enable", 1)
        # self.commandMotor(2, "Torque_Enable", 1)
        # self.commandMotor(3, "Torque_Enable", 1)filt

        # self.commandMotor(1, "Max_Position_Limitfilt
        # self.commandMotor(2, "Max_Position_Limitfilt
        # self.commandMotor(3, "Max_Position_Limit", 1500)

        # self.motor_sub = rospy.Subscriber(
        #   "/dynamixel_workbench/dynamixel_state", DynamixelStateList, self.UpdateMotorsData)

        # Note that "assert" statements do not execute if the optimisation is
        # requested (compiled). The assert statements are there to make sure
        # that an impossible contidion isn't true. Thats why we explicitly
        # check for invalid configuration given that would produce wrong
        # computed commands
        if not self.motor_range['x']['minPosMot'] <= self.motor_range['x']['homeMot'] <= self.motor_range['x']['maxPosMot']:
            raise AssertionError
        if not self.motor_range['y']['minPosMot'] <= self.motor_range['y']['homeMot'] <= self.motor_range['y']['maxPosMot']:
            raise AssertionError
        if not self.motor_range['z']['minPosMot'] <= self.motor_range['z']['homeMot'] <= self.motor_range['z']['maxPosMot']:
            raise AssertionError
        if not self.motor_range['x']['minPosAng'] <= self.motor_range['x']['homeAng'] <= self.motor_range['x']['maxPosAng']:
            raise AssertionError
        if not self.motor_range['y']['minPosAng'] <= self.motor_range['y']['homeAng'] <= self.motor_range['y']['maxPosAng']:
            raise AssertionError
        if not self.motor_range['z']['minPosAng'] <= self.motor_range['z']['homeAng'] <= self.motor_range['z']['maxPosAng']:
            raise AssertionError

    def shutdown_hook(self):
        self.timer.shutdown()

    def connect(self, event):
        """[summary]

        Arguments:
            event {[type]} -- [description]
        """

        try:
            rospy.wait_for_service(
                '/dynamixel_workbench/dynamixel_command', 0.1)
            self.motor_proxy = rospy.ServiceProxy(
                '/dynamixel_workbench/dynamixel_command', DynamixelCommand, persistent=True)
            self.timer.shutdown()
            print("MOTORS FOUND")
        except:
            self.motors = 0
            print("WAITING FOR DYNAMIXEL MOTORS")

    def home(self):
        """[summary]
        """
        for i in range(0, 3):
            self.commandMotor(i+1, "Goal_Position", setHome[i])

    def moveMotor(self, id, pos):
        """[summary]

        Arguments:
            id {[type]} -- [description]
            pos {[type]} -- [description]
        """

        if (pos < setHome[id-1]-setRange[id-1]/2):
            self.commandMotor(id, "Goal_Position",
                              setHome[id-1]-setRange[id-1]/2)
            # print("moveMotor under")
        elif (pos > setHome[id-1]+setRange[id-1]/2):
            self.commandMotor(id, "Goal_Position",
                              setHome[id-1]+setRange[id-1]/2)
            # print("moveMotor over")
        else:
            self.commandMotor(id, "Goal_Position", pos)
            # print(pos)
            # print("moveMotor normal")

    def commandMotor(self, id, command, value):
        """Sends a command to a motor specified by its ID.

        Arguments:
            id {int} -- ID of the motor. Must match the dynamixel motor's id.
            command {[type]} -- [description]
            value {[type]} -- [description]
        """

        # rospy.wait_for_service('/dynamixel_workbench/dynamixel_command') # Only at initialisation
        # try:

        request = DynamixelCommandRequest()
        request.id = id
        request.addr_name = command
        request.value = value
        try:
            self.motor_proxy(request)
            print self.x, self.y, self.z

        except rospy.ServiceException, e:
            print "Service call failed: %s" % e
            print("Error here")

    def callbackXbox(self, Xbox):
        """[summary]

        Arguments:
            Xbox {[type]} -- [description]
        """
        # Only process control if the current source is given to Xbox
        if (self.currentSource == Source.Xbox):

            # Send Xbox commands only when the deadman switch is held on.
            if(Xbox.deadman == 1):
                if(Xbox.home == True):
                    self.home()
                else:
                    if(Xbox.axis.z != self.z):
                        self.moveMotor(1, Xbox.axis.z)
                        self.z = Xbox.axis.z
                    if(Xbox.axis.x != self.x):
                        self.moveMotor(2, Xbox.axis.x)
                        self.x = Xbox.axis.x
                    if(Xbox.axis.y != self.y):
                        self.moveMotor(3, Xbox.axis.y)
                        self.y = Xbox.axis.y

        self.cellOn = Xbox.cellOn

    def callbackHMI(self, data):
        """[summary]

        Arguments:
            data {[type]} -- [description]
        """
        print "hmimsg called"
        if (self.currentSource == Source.Hmi):
            print "hmi msg:", data
            if(data.axis.z != self.z):
                self.moveMotor(1, data.axis.z)
                self.z = data.axis.z
            if(data.axis.x != self.x):
                self.moveMotor(2, data.axis.x)
                self.x = data.axis.x
            if(data.axis.y != self.y):
                self.moveMotor(3, data.axis.y)
                self.y = data.axis.y

        return

    def callbackCtrlSrc(self, data):
        """Processes the current source input set by the HMI.

        Arguments:
            data {ControlSource} -- Contains the source number that should take the control 
        """

        print "source act:", self.currentSource, "new:", data
        if (data.source == data.SOURCE_HMI):
            self.currentSource = Source.Hmi

        elif (data.source == data.SOURCE_XBOX):
            self.currentSource = Source.Xbox

        elif (data.source == data.SOURCE_MOBILE):
            self.currentSource = Source.Mobile

        else:
            self.currentSource = Source.Xbox

        return

    def callbackMobile(self, data):
        """[summary]

        Arguments:
            data {[type]} -- [description]
        """

        if (self.currentSource == Source.Mobile):
            # print "oui"

            euler_or = self.quat_to_euler(data.orientation)
            self.move_to_xyz(euler_or['roll'],
                             euler_or['pitch'], euler_or['yaw'])
        return

    def quat_to_euler(self, orientation):
        """[summary]

        Arguments:
            orientation {[type]} -- [description]

        Returns:
            [type] -- [description]
        """

        x = orientation.x
        y = orientation.y
        z = orientation.z
        w = orientation.w

        # roll = atan2(2*(x*y+z*w), 1-(2*(y**2+z**2)))
        # pitch = asin(2*(x*y-z*w))
        # yaw = atan2(2*(x*w+y*z), 1-(2*(z**2+w**2)))

        test = x * y + z * w

        if (test > 0.499):
            yaw = 2 * atan2(x, w)
            pitch = pi / 2
            roll = 0

            euler1 = [pitch, roll, yaw]
            return euler1

        if (test < -0.499):
            yaw = -2 * atan2(x, w)
            pitch = -pi / 2
            roll = 0
            euler2 = [pitch, roll, yaw]
            return euler2

        sqx = x * x
        sqy = y * y
        sqz = z * z
        yaw = atan2(2 * y * w - 2 * x * z, 1 - 2 * sqy - 2 * sqz)
        pitch = asin(2 * test)
        roll = atan2(2 * x * w - 2 * y * z, 1 - 2 * sqx - 2 * sqz)

        # euler = [pitch, roll, yaw]
        angles = {'roll': roll, 'pitch': pitch, 'yaw': yaw}

        return angles

    def move_to_xyz(self, x_roll_angle, y_pitch_angle, z_yaw_angle):
        """All angles are in radians

        Arguments:
             x_roll_angle {double} -- [description]
             y_pitch_angle {double} -- [description]
             z_yaw_angle {double} -- [description]
        """
        # print "angle in", x_roll_angle, y_pitch_angle, z_yaw_angle
        # Make sure that we at least have a number as an angle
        x_roll_angle = float(x_roll_angle)
        y_pitch_angle = float(y_pitch_angle)
        z_yaw_angle = float(z_yaw_angle)
        # print "angle float", x_roll_angle, y_pitch_angle, z_yaw_angle

        # Creating a local copy to minimise calls to class member
        motx = self.motor_range['x']
        moty = self.motor_range['y']
        motz = self.motor_range['z']

        # Clipping invalid results, or interpolating and creating a motor
        # command. (With angle * delta_motorPos/delta_angle)
        if (x_roll_angle > motx['maxPosAng']):
            x_cmd = int(motx['maxPosMot'])
        elif (x_roll_angle < motx['minPosAng']):
            x_cmd = int(motx['minPosMot'])
        else:
            angle = x_roll_angle - motx['minPosAng']
            delta = (motx['maxPosMot']-motx['minPosMot']) / \
                (motx['maxPosAng']-motx['minPosAng'])
            x_cmd = int(round(angle*delta + motx['minPosMot'], 0))

        if (y_pitch_angle > moty['maxPosAng']):
            y_cmd = int(moty['maxPosMot'])
        elif (y_pitch_angle < moty['minPosAng']):
            y_cmd = int(moty['minPosMot'])
        else:
            angle = y_pitch_angle - moty['minPosAng']
            delta = (moty['maxPosMot']-moty['minPosMot']) / \
                (moty['maxPosAng']-moty['minPosAng'])
            y_cmd = int(round(angle*delta + moty['minPosMot'], 0))

        if (z_yaw_angle > motz['maxPosAng']):
            z_cmd = int(motz['maxPosMot'])
        elif (z_yaw_angle < motz['minPosAng']):
            z_cmd = int(motz['minPosMot'])
        else:
            angle = z_yaw_angle - motz['minPosAng']
            delta = (motz['maxPosMot']-motz['minPosMot']) / \
                (motz['maxPosAng']-motz['minPosAng'])
            z_cmd = int(round(angle*delta + motz['minPosMot'], 0))
            # print delta, z_cmd

        # Making sure that the motor commands are valid. Note that assert
        # statements do not execute if the optimisation is requested (compiled)
        # The assert statements are there to make sure that an impossible
        # contidion isn't true.
        # assert motx['minPosMot'] <= x_cmd <= motx['maxPosMot']
        # assert moty['minPosMot'] <= y_cmd <= moty['maxPosMot']
        # assert motz['minPosMot'] <= z_cmd <= motz['maxPosMot']

        print "x", x_roll_angle, x_cmd  # , motx
        print "y", y_pitch_angle, y_cmd  # , moty
        print "z", z_yaw_angle, z_cmd  # , motz

        # On second thought, to make the system catch internal error, let's make
        # sure the tests are checked even when optimisation is on.
        if not motx['minPosMot'] <= x_cmd <= motx['maxPosMot']:
            raise AssertionError, "Motor command about to be sent is out of bounds"
        if not moty['minPosMot'] <= y_cmd <= moty['maxPosMot']:
            raise AssertionError, "Motor command about to be sent is out of bounds"
        if not motz['minPosMot'] <= z_cmd <= motz['maxPosMot']:
            raise AssertionError, "Motor command about to be sent is out of bounds"

        # print "x", x_roll_angle, x_cmd
        # print "y", y_pitch_angle, y_cmd
        # print "z", z_yaw_angle, z_cmd

        self.moveMotor(1, z_cmd)
        self.moveMotor(2, y_cmd)
        self.moveMotor(3, x_cmd)
        # pass

    def callbackMobile2(self, vector3data):

        if (self.currentSource == Source.Mobile):
            factor = 1
            self.gyropos[0] += factor*vector3data.x
            self.gyropos[1] += factor*vector3data.y
            self.gyropos[2] += factor*vector3data.z

            motx = self.motor_range['x']
            moty = self.motor_range['y']
            motz = self.motor_range['z']

            if (self.gyropos[2] < setHome[0]-setRange[0]/2):
                self.gyropos[2] = setHome[0]-setRange[0]/2
            elif (self.gyropos[2] < setHome[0]+setRange[0]/2):
                self.gyropos[2] = setHome[0]+setRange[0]/2

            if (self.gyropos[0] < setHome[1]-setRange[1]/2):
                self.gyropos[0] = setHome[1]-setRange[1]/2
            elif (self.gyropos[0] < setHome[1]+setRange[1]/2):
                self.gyropos[0] = setHome[1]+setRange[1]/2

            if (self.gyropos[1] < setHome[2]-setRange[2]/2):
                self.gyropos[1] = setHome[2]-setRange[2]/2
            elif (self.gyropos[1] < setHome[2]+setRange[2]/2):
                self.gyropos[1] = setHome[2]+setRange[2]/2

            print self.gyropos
            # self.moveMotor(1, self.gyropos[2])
            # self.moveMotor(2, self.gyropos[0])
            self.moveMotor(3, self.gyropos[1])

        pass


if __name__ == '__main__':
    """[summary]
    """

    try:
        rospy.init_node('main', anonymous=True)
        mc = main_control()
        rospy.spin()
        # Tests:
        # mr = motor_range()
        # print mr.motor_range['x']
        # print mr.motor_range['y']
        # print mr.motor_range['z']

        # mr.move_to_xyz(-1.2234, 0.1, '0')
        # mr.move_to_xyz(56, 0.24, 2345.2)
        # # mr.move_to_xyz("324",{'x':23.4}, (-0.62))
        # # mr.move_to_xyz("", 'a', [0.4])
    except rospy.ROSInterruptException:
        pass

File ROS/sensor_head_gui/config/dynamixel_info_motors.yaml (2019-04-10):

# You can find control table of Dynamixel on emanual (http://emanual.robotis.com/#control-table)
# Control table item has to be set Camel_Case and not included whitespace
# You are supposed to set at least Dynamixel ID
zaxis:
  ID: 1
  # Torque_Enable: 0
  # Velocity_limit: 120
  Profile_Velocity: 0 # Maximum 10?
  Return_Delay_Time: 0
  Min_Position_Limit: 0
  Max_Position_Limit: 4095
  Operating_Mode: 3 # Position control mode
 
xaxis:
  ID: 2
  Return_Delay_Time: 0
  Min_Position_Limit: 0
  Max_Position_Limit: 1365
  Operating_Mode: 3 # Position control mode
  #Profile_Velocity: 100
yaxis:
  ID: 3
  Return_Delay_Time: 0
  Min_Position_Limit: 0
  Max_Position_Limit: 1535
  Operating_Mode: 3 # Position control mode
  #Profile_Velocity: 100

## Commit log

2019-01-16 Upload first cad model
    Add assy of first iteration of base
    [3axis assy_2.0.SLDASM, XL-430_2.0.SLDASM]
2019-01-16 Added a bash script containing the commands entered to configure the Raspberry Pi
2019-01-23 Cads Z and X axis
    [535198.STEP, 535198.step.SLDPRT, 545404.STEP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]
2019-01-23 travail du 23 janvier
    [615406 assembly.STL, Cover.STL, Cover.sldprt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]
2019-01-30 Y axis CAD
    [0.25 Bore Bottom Tapped Clamping Mount.SLDASM, Pattern Set Screw Hubs.SLDASM, Spacers_0.25.SLDPRT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]
2019-01-30 Y axis CAD V1.2
    [Cover.STL, X_base_3.0.sldprt, X_base_3.STL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]
2019-02-03 work of 2/2/2019
    [0.25 Bore Bottom Tapped Clamping Mount.SLDASM, 3axis assy_2.0.SLDASM, 535198.STEP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]
2019-02-06 Cleanup Assy
    [0.25 Bore Bottom Tapped Clamping Mount.SLDASM, 0.25_hub.SLDPRT, 545548 assy.SLDASM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]
2019-02-06 Y axis folder
    [Y_Assy.SLDASM]
2019-02-14 Update README.md with Arduino IDE install instructions
2019-02-14 New cad and update hardware
    Merge
    [0.25 Bore Bottom Tapped Clamping Mount.SLDASM, 3axis assy_2.0.SLDASM, 535198.STEP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]
2019-02-20 Update sensor_head_hmi PY and UI files
2019-02-20 BOM MAJ
    [BOM.xlsx, Master_parts_list.xlsx, adapter moteur-gear.STL]
2019-02-20 Renamed folder and package to sensor_head_gui
2019-02-21 Creating a launch file by including the dynamixel_workbench launch file
    However, the motor configuration yaml doesn't seem to be changable by arguments. Will create directly a new node instead.
    [dynamixel_info_motors.yaml]
2019-02-21 Moved the inline yaml to a separate file
    Moved the inline yaml to a separate file so that xml formatters don't break the parameters by adding tabs.
    [dynamixel_controller_params.yaml]
2019-02-21 Adjusted the labels and motor names, the enable button on load, send position command from the same function
2019-02-21 Re: adjusted the labels and motor names, the enable button on load, send position command from the same function
2019-03-13 Publishing the orientation and motion as a IMU message to the mobile_imu topic
2019-03-20 Using USB camera, serving it through HTTP, and using it in the web page
2019-03-20 Initial class of Manual Control
    WIll have to test with motors
2019-03-20 Tried different settings on the raspberry pi
2019-03-27 Fixed lists of buttons and axes
2019-03-27 cad update
    [625104 assembly.STEP, Coupler_MoteurV2.STL, Coupler_MoteurV2.sldprt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]
2019-03-27 (not working) corrected manual_control and changed messages
    [manual_control.py]
2019-03-27 firts version of Filter
2019-04-04 Update Cover_OpenCR_CASE.SLDPRT
    open cr case update
    [Cover_OpenCR_CASE.SLDPRT]
2019-04-04 Update Bom
    [BOM.xlsx, Master_parts_list.xlsx]
2019-04-04 Filter for the position of the cellphone
2019-04-04 Final version Filter for the position of the camera
2019-04-04 fixed typo in python
    [manual_control.py]
2019-04-04 Fixed accents in comments that caused an error when executing
    [main_control.py, manual_control.py]
2019-04-04 open cr update
    [CCR10_OpenCR_REVF1.STL, CaseOpenCR.STL, CaseOpenCR.sldprt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]
2019-04-05 baselaunch include dynamixel motor
2019-04-05 desactivate temporarly gui and run motors
2019-04-05 commit de fin de session de travail(gros delais)
2019-04-06 Added the motor's range in the config at start
    [dynamixel_info_motors.yaml]
2019-04-06 Trying to speed the delay of command to motor
2019-04-06 Added motor operating mode
    [dynamixel_info_motors.yaml]
2019-04-07 Converting angle commands to motor commands
2019-04-07 Made python scripts executable so they can be launched with roslaunch without unknown problems
    [sensor_head_hmi.py, sensor_head_hmi_plugin.py]
2019-04-07 Adjusted some values, and added self.x, y, z to main control. Worked on pi
    [dynamixel_controller_params.yaml]
2019-04-07 Corrected max/min controller values
    [manual_control.py]
2019-04-07 Filter of quaternions normalzed and initialized to unit quaternion
2019-04-07 desactivated joint state on motor controller?
2019-04-07 Updated controller functions
    [dynamixel_controller_params.yaml, dynamixel_info_motors.yaml]
2019-04-07 COnnected mobile imu to quat_to_euleur
2019-04-07 Recoded motor ranges
2019-04-07 typo in sensor_msgs math import
2019-04-07 Fixed once again the atan2
    [main_control.py]
2019-04-07 Once again tried to fix the atan2
    [main_control.py]
2019-04-07 fixed names and moveto
    [main_control.py]
2019-04-07 Activating the filter of angle
2019-04-07 forgot the shebang on the filter file
2019-04-07 All 3 motors run at the same time with controller
2019-04-07 queue_size of publisher filter
2019-04-08 Added A button
2019-04-08 added the button enable for cell
2019-04-08 Changed axis limits of x axis
    [dynamixel_info_motors.yaml]
2019-04-08 initializing timer member to someting
2019-04-08 typo in motor configuration
    [dynamixel_info_motors.yaml]
2019-04-08 revert removing__init__ of hmi code
    [sensor_head_hmi.py]
2019-04-08 Corrected GUI homing button action connected
    [sensor_head_hmi.py]
2019-04-08 Message to receive the current ControlSource
2019-04-08 Corrected typos for running HMI with changes Co-authored-by: Etienne Gendron <40276552+gene2302@users.noreply.github.com>
    [main_control.py, sensor_head_hmi.py]
2019-04-09 Homing function seems to work
2019-04-09 filter 20 donné
2019-04-09 filter 20 donner
2019-04-09 Added a web manifest and repaired mobile control orientation errors
    [main_control.py]
2019-04-09 Correct controller delay (not tested)
    [manual_control.py]
2019-04-09 adjust rate xbox
    [dynamixel_info_motors.yaml]
2019-04-09 inverse x axis command
2019-04-10 start camera
2019-04-10 relative sensor
2019-04-10 x motor
2019-04-10 add y motor
2019-04-10 try to use gyroscope
2019-04-10 added ove motor
2019-04-10 only activate if current source
2019-04-10 comment hmi code
    [Master_parts_list.xlsx]
